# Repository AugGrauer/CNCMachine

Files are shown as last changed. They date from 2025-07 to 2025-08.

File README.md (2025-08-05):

# CNCMachine
Open source repository for the CNC machine built by [Backyard Shed Engineering](https://www.youtube.com/@ShedStuffBuiltHere)



This is a fully self-funded, opensource project done by two highschoolers. While we have tried our best to document everything, and make it as accessible as we can, there is still an aspect of DIY to this project. Before building, please study the CAD models provided. If you run into problems, open an issue and we will try to respond and improve this guide.

This machine is mostly 3D printed. 3D printer access is required. 
## License


Feel free to use this as a basis for your own project, or replicate it!

## Table of Contents
- [Specifications](#specifications)
- [License](#license)
- [BOM](#bom)
- [Use](#use)
- [Known Issues](#known-issues-)
- [Assembly](#assembly)
- [CAD Models](#cad-models)
- [Wiring](#wiring)
- [Firmware/Software](#firmwaresoftware)
- [Putting it all together](#putting-it-all-together)
- [Media](#media)
- [Contributing](#contributing-)
- [Roadmap](#roadmap)
- [Changelog](#changelog)
  
## Specifications

  Build Area: 16x18x1 in 

  Total Footprint: 
  
  Supported Materials: Aluminium, wood, plastics. (Anything softer than aluminium)

  Motors: 3x NEMA 23, 1x NEMA 17 

  Spindle: Choice Spindle/Router/VFD. Designed for a Dewalt Trim Router. Easily Modified for a Makita 1 1/4HP Router

  Control Board: Arduino UNO w/ GRBL 1.1
  
  Power Requirements: 120V

## BOM
BOM is in the repository and also here:
https://docs.google.com/spreadsheets/d/1JcS2ukq2nQpIpGEV6_Kvxhg6B4QogmMNbcgQQ2et4MQ/edit?usp=sharing

# Use
  We have created this repository in order to make our CNC project as open source as possible. We were really proud to do this project for under $1000, and we want others to be able to as well. Feel free to use this as a basis to design your own, or to simply make your own version of our machine. We have included the BOM, all of our 3D models used, and our wiring diagram, as well as a few extra resources and our advice. We have further explanations on our youtube channel. ⏯️

## Known Issues 🐛
  This machine is by no means perfect, so there are a few problems we have encountered. Below is a list of the problems and if we have found solutions
  1. Electromagnet Interference: ✅
     - This is probably the largest issue encountered during construction and inital operation. After investigating, it turns out that our buildplate, and most metal on the body of the CNC machine is actually charged. We aren't sure why or from where, but we suspect that it is something to do with our stepper motors.
     ### **FIX**
       - To fix this, we used EMI shielding along most of the long wires which run from stepper motors to the electrical box. This is included in the BOM, and we had just enough to get most of our wires shielded. We found that there were a few specific areas which were worse, especially where the EMI shielding/ wires in general come in contact with the metal frame of the machine. We solved this by insulating those specific areas with electrical tape.
  2. Bed Leveling 🟠
     - We have been unable to really solve this. It isn't a terrible issue, and certainly doesn't prevent the operation of the machine. Take this into account when slicing models/preparing to cut stuff, as there may be a few corners (at least for us) which dont cut all the way to the buildplate. By using an overcut, you can compensate for this.
      ### **FIX**
       - We don't have a 100% fix, but if you plan to overcut by .1/.2mm, everything should cut through. If you don't want to do that, it is pretty easy to break the last little layer off and get a clean part.
  3. Alarms ✅
     - This machine alarms a decent amount. Don't be too alarmed (See what I did there). If you are using UGS/GRBL like we did, you can reset and unlock the machine to continue. Usually alarms occur due to a voltage change, or a serious problem. After frequent use and learning, we found that most of our alarms occur when turning on the router. This is pretty easy to work with, as we just reset and continue. If your machine is constantly alarming, test it for voltage differences/charges in weird places. Try insulating. The limit switches are USUALLY not actually the problem.
      ### **FIX**
       - Reset and unlock machine. If that doesn't work, test and insulate/ground different areas. Limit switches are pretty reliable for us, so that was almost never the issue.
  4. Soft Limits ✅
     - These never worked on our machine. We don't know why. We just don't use them.
      ### **FIX**
       - Don't use
  5. Weird GCode ✅
     - There are a few weird little GCode quirks that we have to deal with to operate. Shown here is what the start and end of our GCode looks like. This works. Obviously it will be different depending on position, tool, etc but the start and end remain the same. Make sure your code looks similar/the same, as you run the risk of breaking a bit if not. If it looks different, I'd suggest running the code without a bit, to ensure nothing will break before cutting.
### START
```
  (10022) # Program number (Changes)
  G90 G94
  G17
  G21
  (Ramp1) #This will be different depending on your action
  T1
  S5000 M3
  G17 G90 G94
  G54
  G0 Z15 #This is critical. This MUST be before the following line. This retracts the toolhead BEFORE moving XY
  G0 X-28.057 Y-2.102 # this changes
```
### END
```
G0 Z15
    # Usually there is an extra line here. Make sure to delete that, as it homes the machine, which can break bits. 
M30
```
  ### **FIX**
  - Change GCode every time. You could also write a program to do this. We will share that if we end up doing this.

## Assembly 

  DISCLAIMER:
  
  We tried to document roughly our steps in the videos on our channel, but there are a lot of nuances and tricks needed that simply arent documented. Be prepared for sanding, and some weird assemblies. In order to cut aluminium, we had to manually machine multiple parts, such as the Z axis plates, the entire aluminium base of the buildplate, and the Z traveller mount. We do not recommend this for entry level builds. If you have some time, a 3D printer, and some experience in the STEM/3D printing fields, this is very doable. All of the parts we used are in the BOM, and if you follow the 3D model, it should be pretty straight forward. It took us a total of 35 hours to build this machine, but we were doing other things and not 100% focused for much of it, in addition to having to test multiple parts. If you have questions, reach out to us via youtube, or create an issue here. We recommend looking at some youtube tutorials for parts you don't quite understand. There are great ones which let us teach ourselves GRBL and Fusion 360 manufacturing/slicing. 

## **We have created a guide which outlines the assembly as best we can. Find it in AssemblyGuide.md**

Use this guide, with the 3D model, youtube videos, and 3d model guide, to get the best idea of how to build this.

  A few notes.
  - Screws are mostly M4. The rails use M5x16 screws, and there are a few random M3 screws in there, but the majority are M4.

### CAD Models:
  [Found Here](https://github.com/AugGrauer/CNCMachine/tree/c9973d6ad02c3cf29ccf315ba2bd43aa739bddab/3D%20Models](https://github.com/AugGrauer/CNCMachine/tree/823ef2db97a0531feb1171109dd2441a3dbac2b9/3D%20Models))
  
  Our CAD models are categorized by:
  - Imports (This is largely just parts we used to build the machine)
  - Parts (Actual parts we made which were either machined or cut)
  - Assemblies (Larger models, such as the Base and Z axis)
  
### Wiring:
[Found Here](https://github.com/AugGrauer/CNCMachine/tree/c9973d6ad02c3cf29ccf315ba2bd43aa739bddab/Wiring](https://github.com/AugGrauer/CNCMachine/tree/823ef2db97a0531feb1171109dd2441a3dbac2b9/Wiring))

  We have provided our wiring diagram above. We also created a custom electrical box for these wires, but that is entirely optional. See docs in wiring folder for more info. 
  
### Firmware/Software:
  This machine runs off of GRBL and Universal GCode Sender. Below are the downloads:

  [GRBL](https://github.com/grbl/grbl)

  [UGS](https://winder.github.io/ugs_website/)

  We changed our GRBL config file before uploading to the Arduino. Make sure to get all the pin numbers correct. (Found in cpu_map.h)
  
  For UGS, we did not change much. Go through the Setup Wizard and ensure your machine passes all checks. Be sure to test limit switches and tune steps/mm for the steppers.

### Putting it all together:
  When it comes down to it, theres a few key steps to follow:
  
1. Order/Print parts
2. Assemble hardware
3. Wire based off of our guide
4. Flash GRBL
5. Troubleshoot and Test UGS

Follow AssemblyGuide.md but if you have questions, please create an issue here, leave a comment on our videos, or even email us.

Here is the link our video playlist explaining it: https://www.youtube.com/watch?v=x9RqWOT4NOQ&list=PLWdkqCAyfFqSBZGNOKGVb3XG4A6ohDbLp

## Media

CAD:

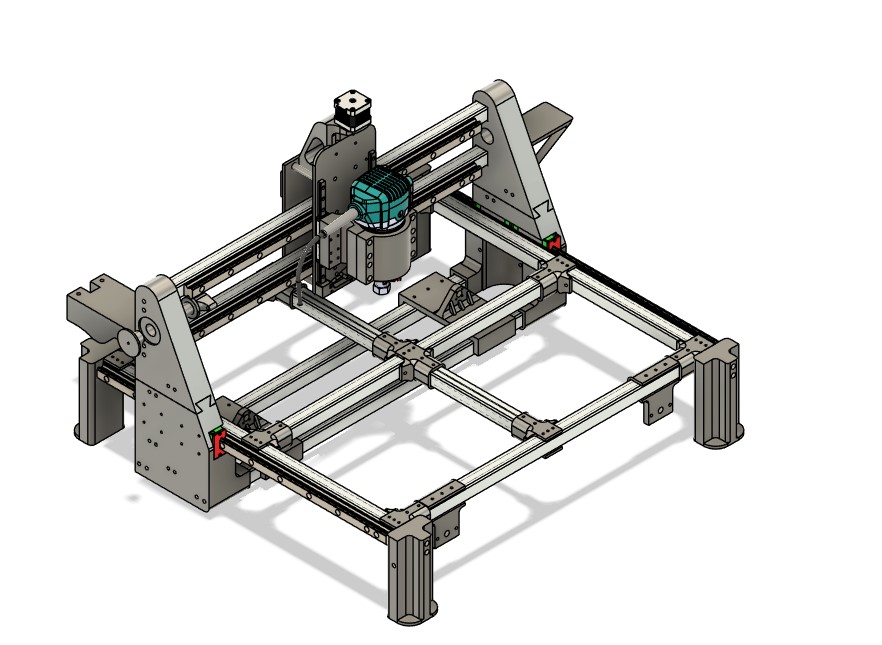
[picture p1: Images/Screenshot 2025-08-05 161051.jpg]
/Images/Screenshot 2025-08-05 161051.jpg)
)

Base:

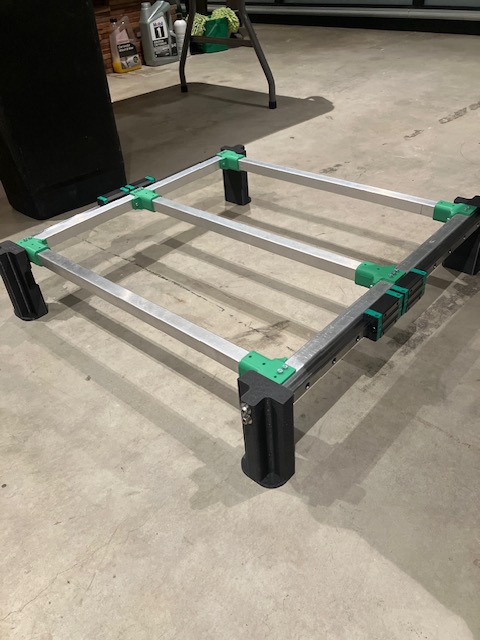
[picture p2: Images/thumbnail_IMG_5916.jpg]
base


In Progress:

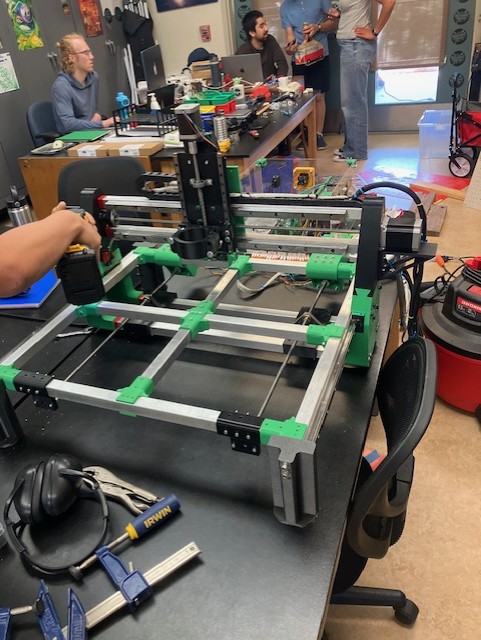
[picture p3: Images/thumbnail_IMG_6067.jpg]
progress


Full build:

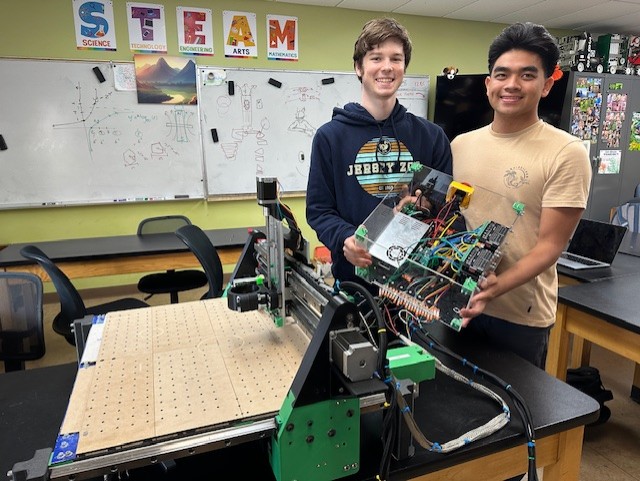
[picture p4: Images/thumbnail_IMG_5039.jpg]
full)


## Contributing 🔨
  We welcome any progress, changes, and suggestions. We definitely want to improve and build upon both this machine and open source project.

## Roadmap
  - Design Dust collection/cleaning system
  - Automate spindle cooling/oil dripping
  - Explore VFD possibilites
  - Create a GCode Pre-processor to speed up work

## Changelog
  # V 1.0
  - Initial open-source release
  - Complete with BOM, CAD models, wiring diagrams, and build videos

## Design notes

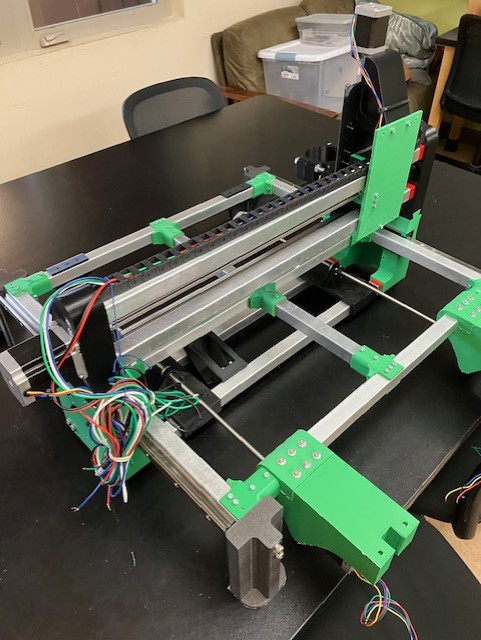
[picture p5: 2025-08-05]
Images/thumbnail_IMG_6022.jpg

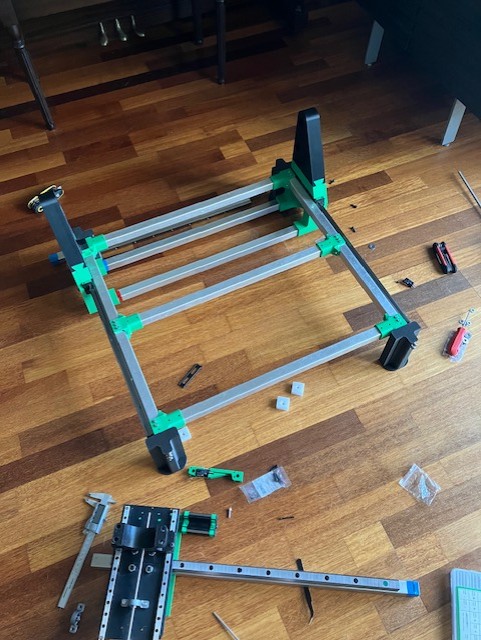
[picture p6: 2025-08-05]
Images/thumbnail_IMG_5942.jpg

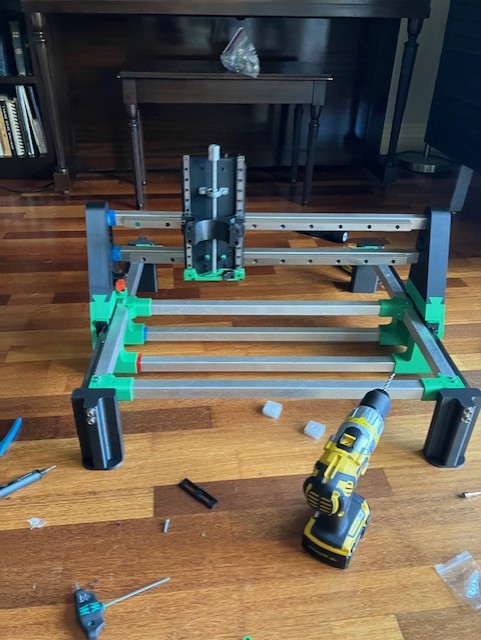
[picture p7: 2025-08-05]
Images/thumbnail_IMG_5947.jpg

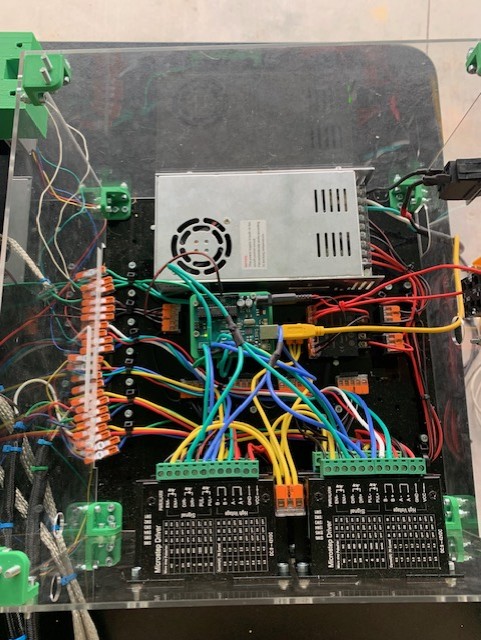
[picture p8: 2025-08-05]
Images/thumbnail_IMG_3427.jpg

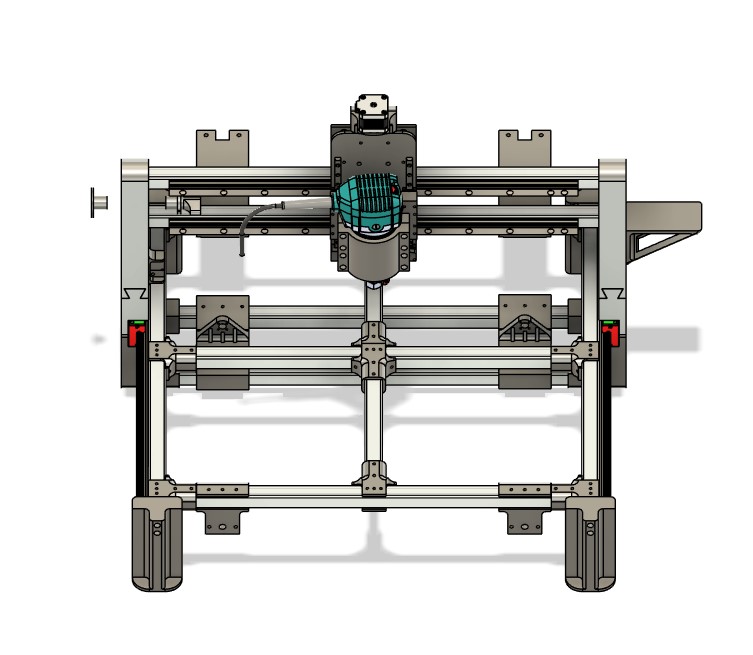
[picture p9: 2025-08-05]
Images/Screenshot 2025-08-05 161105.jpg

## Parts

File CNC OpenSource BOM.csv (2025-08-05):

Item | Supplier | Amount | Price per | Price total | Link | Column 1
NEMA 23 Stepper Motors, Drivers, and PSU | Amazon | 1 | $131.00 | $131.00 | https://www.amazon.com/RATTMMOTOR-Controller-Nema23-Stepper-Control/dp/B09MRYBNTX
250mm Leadscrew | Amazon | 1 | $19.84 | $19.84 | https://www.amazon.com/Vertical-Printer-Bearing-Flexible-Coupling/dp/B0B8WR5R8W?gQT=1&th=1
600mm LeadScrew | Amazon | 2 | $38.70 | $77.40 | https://www.amazon.com/100-600mm-Bearing-Bracket-Flexible-Coupling/dp/B0DMJDKH3Z?gQT=1&th=1
650mm LeadScrew | Amazon | 1 | $20.99 | $20.99 | https://www.amazon.com/ReliaBot-650mm-Thread-Starts-Printer/dp/B092W56RC4?gQT=1
Emergency Stop | Amazon | 1 | $9.99 | $9.99 | https://www.amazon.com/Baomain-Emergency-Switch-Button-Weatherproof/dp/B00NTT91Y0?hvadid=695397056053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
HGR20R 600mm | Amazon | 2 | $50.99 | $101.98 | https://www.amazon.com/Linear-20-600mm-Bearing-Guideway-Routers/dp/B0BKGB99SD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
Limit Switches | Amazon | 1 | $6.39 | $6.39 | https://www.amazon.com/Cylewet-V-156-1C25-Momentary-Arduino-CYT1046/dp/B06WRN7FQB
MGN9 250MM carriage and rails | Amazon | 1 | $28.88 | $28.88 | https://www.amazon.com/gp/product/B09QYMQW5V/ref=ox_sc_act_title_1?smid=A3BJIOXQCA1C52&th=1
Power Step | Amazon | 1 | $9.99 | $9.99 | https://www.amazon.com/EPBOWPT-Converter-Regulator-Voltage-Transformer/dp/B0DPZYH3C7
6061 T651 Aluminum Sheet Metal 12 x 12 x 0.20 (5mm) Inch Flat Plain Aluminum Plate Covered with Protective Film, Heat Treatable Rectangle Aluminum Metal Plate for Crafting, DIY, Industrial | Amazon | 1 | $22.99 | $22.99 | https://www.amazon.com/Aluminum-Protective-Treatable-Rectangle-Industrial/dp/B09JFN8353
1/4 in shank 1/8 in cutting bit | Amazon | 1 | $16.99 | $16.99 | https://www.amazon.com/dp/B0D1DS85TK?ref=ppx_yo2ov_dt_b_fed_asin_title&th=1
Extra Stepper motor driver | Amazon | 1 | $10.89 | $10.89 | https://www.amazon.com/dp/B08SG7L54W?ref=ppx_yo2ov_dt_b_fed_asin_title
Wago Multipack | Amazon | 1 | $14.77 | $14.77 | https://www.amazon.com/dp/B07NKSHVF6?ref=ppx_yo2ov_dt_b_fed_asin_title
16 AWG Wire | Amazon | 1 | $16.99 | $16.99 | https://www.amazon.com/dp/B0CMLFRQDQ?ref=ppx_yo2ov_dt_b_fed_asin_title&th=1
50mm m4 screws | Amazon | 1 | $9.38 | $9.38 | https://www.amazon.com/dp/B089NJRS78?ref=ppx_yo2ov_dt_b_fed_asin_title&th=1
Solid lead screw couplers | Amazon | 2 | $8.99 | $17.98 | https://www.amazon.com/Befenybay-Coupling-Diameter-Coupler-Aluminum/dp/B07WZJSLBL
nema 17 stepper motor | Amazon | 1 | $14.99 | $14.99 | https://www.amazon.com/CNCTOPBAOS-Stepper-2-Phase-17HS4218-Engraver/dp/B09FLG1VPF?xpid=Nh-QG1XuaLlTQ
2 more carriages for z | Amazon | 2 | $10.92 | $21.84 | https://www.amazon.com/KGTCN-Miniature-Sliding-Machine-Printer/dp/B0C3CSKTVN?s=industrial
electromagnetic shielding | Amazon | 1 | $17.99 | $17.99 | https://www.amazon.com/Tinned-Copper-Braided-Sleeving-Diameter/dp/B01BIBQ940
Cable chain | Amazon | 1 | $11.99 | $11.99 | https://www.amazon.com/dp/B07QVKL1H6/?coliid=I1AD8NK504AR2V&colid=39P1VAIP6UUD2
weideer 2322pcs M3 Screw Assortment Kit | Amazon | 1 | $25.99 | $25.99 | https://www.amazon.com/dp/B0DS8HYF64/
Filament 1kg | Amazon | 3 | $20.99 | $62.97 | https://www.amazon.com/Overture-Filament-Professional-Toughness-Dimensional/dp/B07YDN56F2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
Aluminum Composite panel | Amazon | 1 | $35.82 | $35.82 | https://www.amazon.com/Falken-Design-Aluminum-Composite-Brushed/dp/B07NRBGHVB?s=industrial
1501 Series M4 x 0.7mm Standoff (6mm OD, 58mm Length) - 4 Pack | GoBilda | 1 | $5.99 | $5.99 | https://www.gobilda.com/1501-series-m4-x-0-7mm-standoff-6mm-od-58mm-length-4-pack/
1/2 in bar | The Depot | 1 | $13.27 | $13.27 | https://www.homedepot.com/p/Everbilt-1-2-in-x-4-ft-1-8-in-Thick-Plain-Steel-Flat-Bar-0702/332734311
16 AWG wire x4 | The Depot | 4 | $6.63 | $26.52 | https://www.homedepot.com/p/Cerrowire-24-ft-16-Gauge-Red-Stranded-Primary-Wire-207-1203R24/202206417
Switch | The Depot | 1 | $4.96 | $4.96 | https://www.homedepot.com/p/Gardner-Bender-10-Amp-Single-Pole-Illuminated-Rocker-Black-Switch-GSW-49/300349420
Tool repair cord | The Depot | 1 | $16.68 | $16.68 | https://www.homedepot.com/p/Husky-9-ft-14-3-Medium-Duty-Tool-Replacement-Cord-Black-HD-342-576/303679849
M5x16 screws 2pc | The Depot | 12 | $2.25 | $27.00 | https://www.homedepot.com/p/5-mm-0-8-x-16-mm-Internal-Hex-Plain-Steel-Metric-Socket-Cap-Screw-2-Pieces-803288/204274287
Lag Bolts for router clamp | The Depot | 4 | $3.75 | $15.00 | https://www.homedepot.com/p/M8-1-25-x-50-mm-Class-8-8-Zinc-Plated-Hex-Bolt-801718/204273672
Nuts for router clamp | The Depot | 2 | $3.75 | $7.50 | https://www.homedepot.com/p/Everbilt-M8-1-25-Zinc-Metric-Hex-Nut-5-per-Bag-802418/204281770
Wago direct conenctors | The Depot | 1 | $21.97 | $21.97 | https://www.homedepot.com/p/WAGO-221-2401-Lever-Nuts-Inline-2-Wire-Splicing-Connectors-25-Pack-0221240K000-0012/330518029
Peanut Bar 72 in | Other | 3 | $29.00 | $87.00 | https://andymark.com/products/1-x-1-peanut-extrusion-different-lengths?variant=44493385990316 | This gets cut into rougly 2 foot sections
Cut Board (Draftboard) | The Depot | 1 | $6.49 | $6.49 | https://www.homedepot.com/p/ProWood-1-8-in-x-2-ft-x-4-ft-Tempered-Hardboard-Actual-0-115-in-x-23-75-in-x-47-75-in-Project-Panel-109112/202585358
 |  |  | Total | 940.42 | Plus Tax

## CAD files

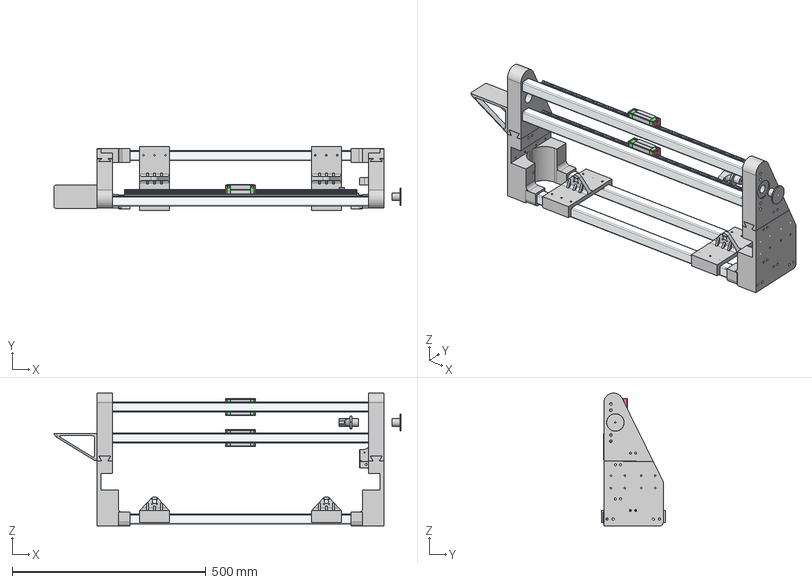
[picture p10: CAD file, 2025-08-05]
3D Models/X/full x gantry model v3.step
895.6 x 165.4 x 343.2 mm
Component1(Mirror)(Mirror) (2)(Mirror)
Component1(Mirror)(Mirror) (2)(Mirror)_1
xAxisMotorMount
am-3090a-2 2ft Peanut x 2
am-3090a-2 2ft Peanut_1 x 2
HGR20R LINEAR GUIDE RAIL, CONFIGURABLE, 600 mm x 2
HGH20CAZ0C, BLOCK, MIDSECTION x 2

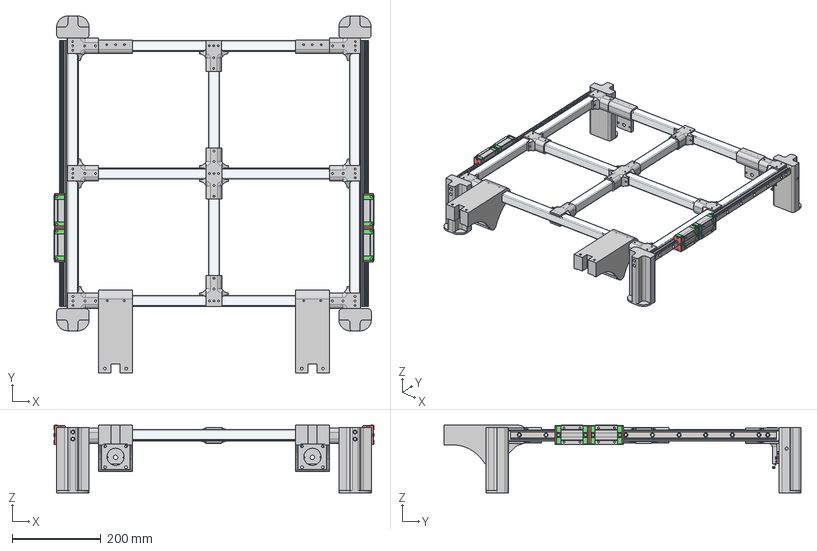
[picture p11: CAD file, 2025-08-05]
3D Models/B/base.step
720.8 x 804.6 x 152.8 mm
Component1(Mirror) (2) x 2
HGR20R LINEAR GUIDE RAIL, CONFIGURABLE, 600 mm
HGR20R LINEAR GUIDE RAIL, CONFIGURABLE, 600 mm_1
HGH20CAZ0C, BLOCK, MIDSECTION x 2
HGH20CAZ0C, BLOCK, MIDSECTION v1(Mirror) x 2
leg3
Cover
Connector - straight x 2
Connector - bent
Switch
Rivet - long
Arm
Roll
Rivet - short
leg3 v7
leg3 v3(Mirror)
leg3 v3(Mirror)(Mirror)
am-3090a-2 2ft Peanut x 2
Component1(Mirror) (1)
am-3090a-2 2ft Peanut_1 x 3
am-3090a-2 2ft Peanut_2 x 2
y leadscrewholder endstop x 2
Component1(Mirror) (3)
Component1(Mirror) (4) x 3
Component1(Mirror) (5)

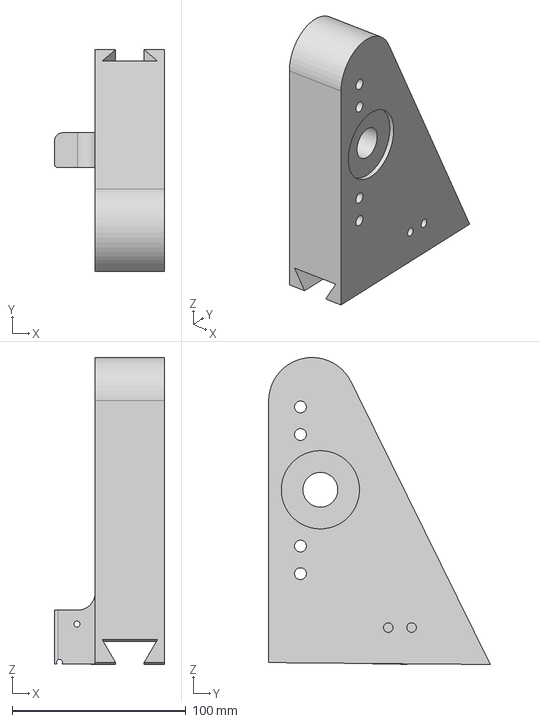
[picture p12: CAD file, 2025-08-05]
3D Models/X/right x wall top v1.step
63.4 x 127.5 x 176.5 mm

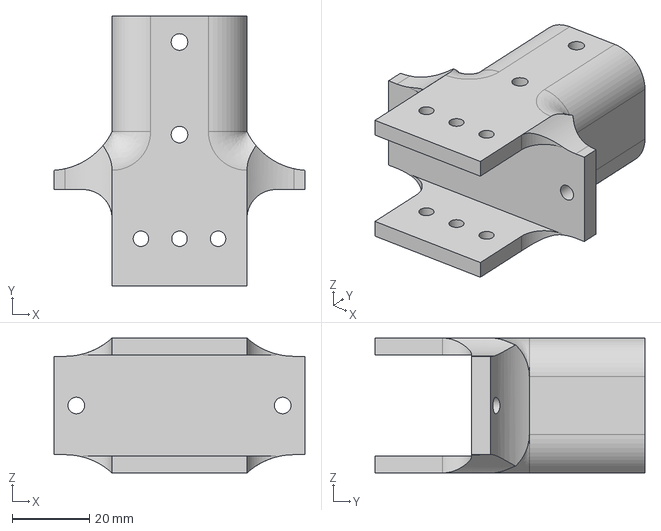
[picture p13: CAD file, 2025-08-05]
3D Models/B/side coupler_.step
65.0 x 70.0 x 35.0 mm

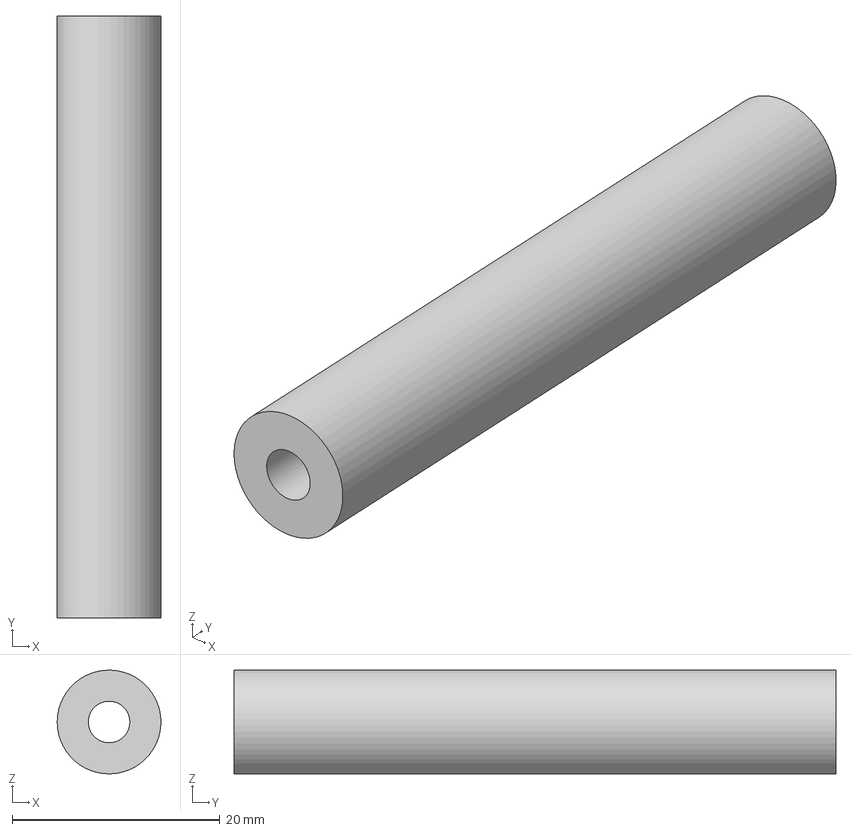
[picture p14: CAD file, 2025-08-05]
3D Models/Z/z spacer (standoffs) v1.step
9.99 x 58.0 x 10.00 mm

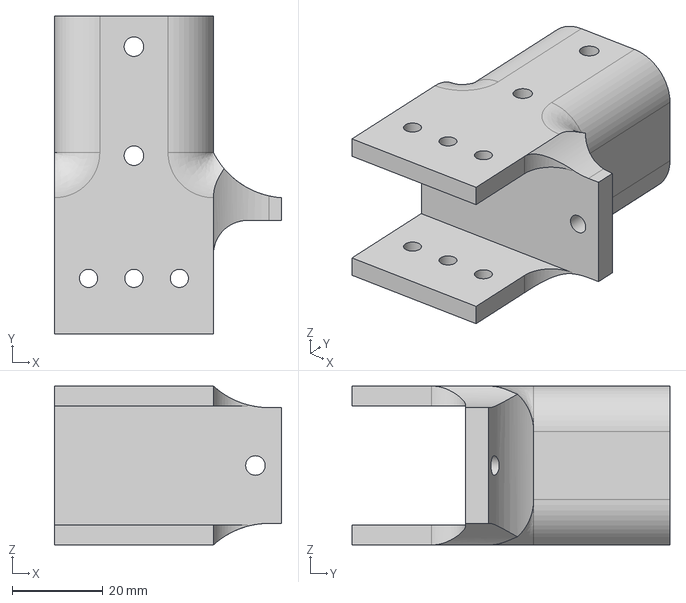
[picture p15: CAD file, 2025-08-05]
3D Models/B/corner coupler_.step
50.0 x 70.0 x 35.0 mm

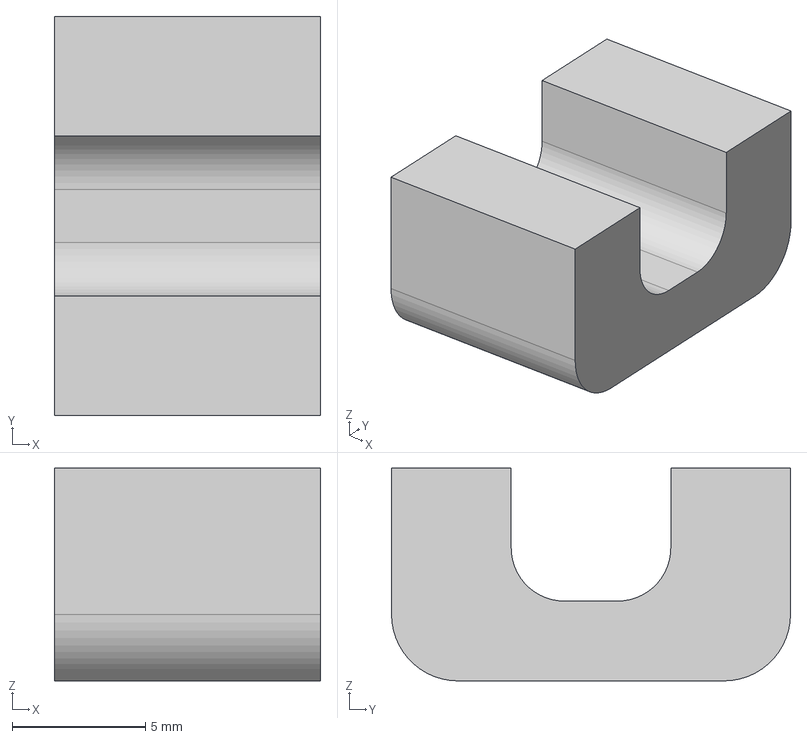
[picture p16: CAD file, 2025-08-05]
3D Models/X/cable holder v4.step
10.0 x 15.0 x 8.00 mm

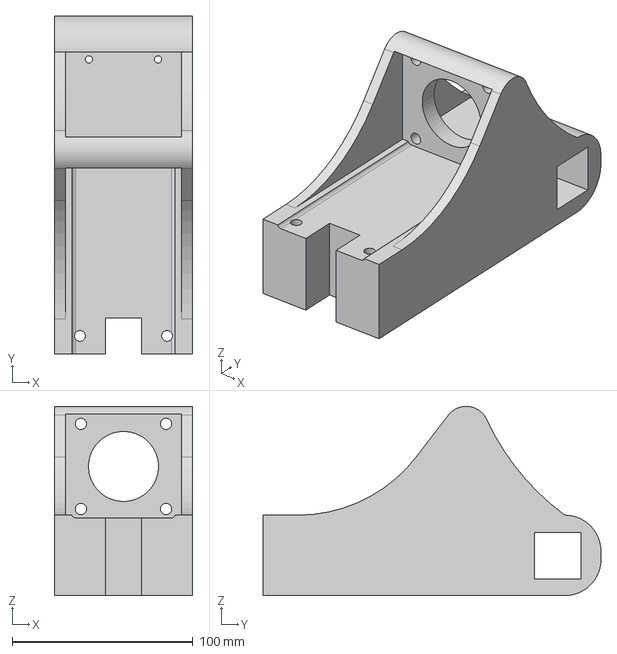
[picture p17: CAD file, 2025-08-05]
3D Models/Y/y motor mount L&R v3.step
76.4 x 186.9 x 104.6 mm

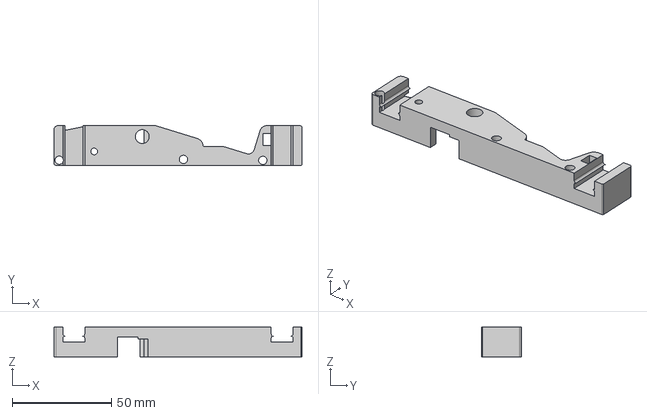
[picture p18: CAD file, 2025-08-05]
3D Models/Z/limit switch holderend stop v1.step
125.0 x 20.0 x 15.0 mm

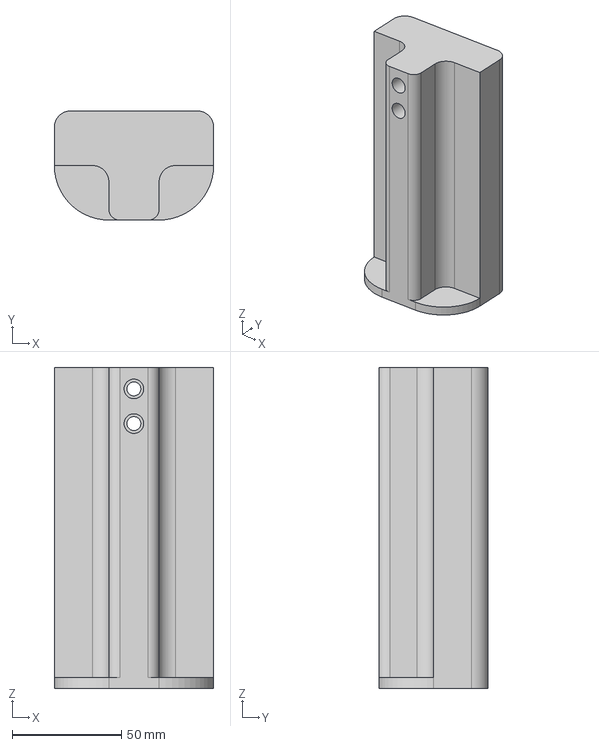
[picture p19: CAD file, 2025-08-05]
3D Models/B/normal leg_.step
73.0 x 50.0 x 147.0 mm

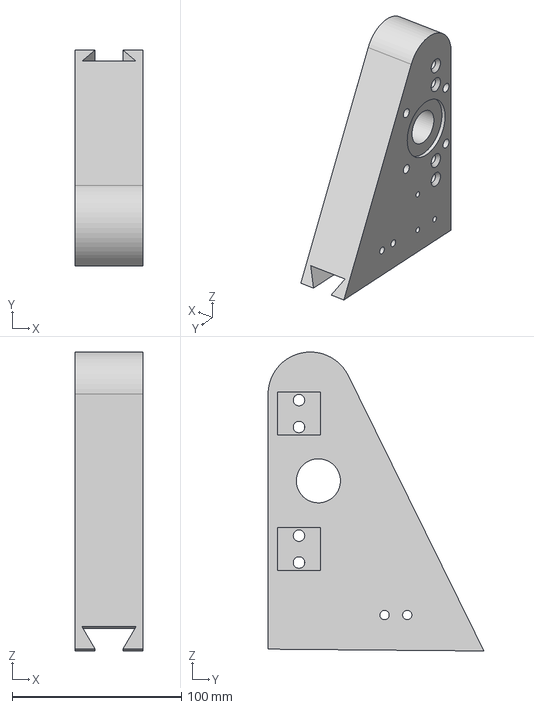
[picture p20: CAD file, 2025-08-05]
3D Models/X/left x wall top v2.step
40.0 x 127.5 x 176.5 mm

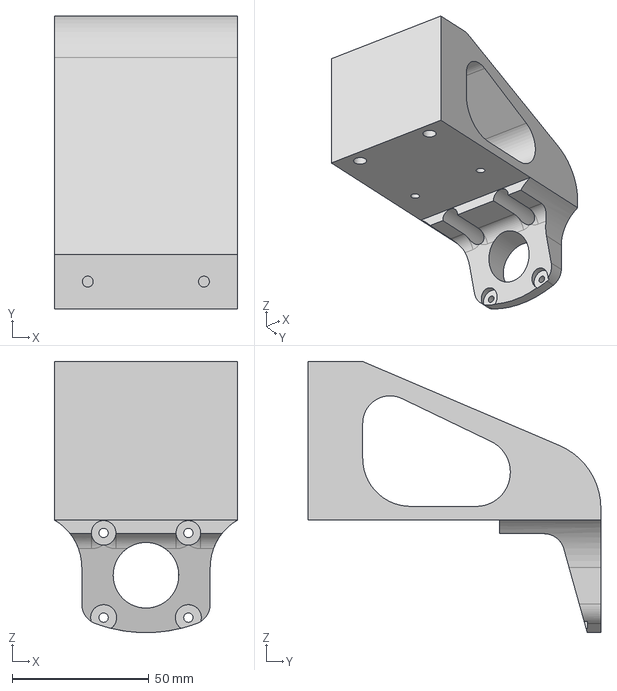
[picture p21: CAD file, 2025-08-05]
3D Models/Z/overhead z stepper motor mount v1.step
67.0 x 107.1 x 99.1 mm

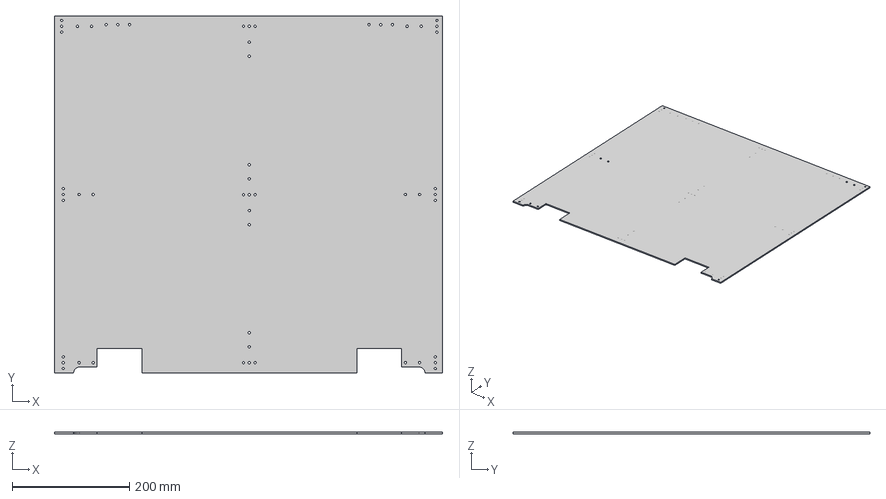
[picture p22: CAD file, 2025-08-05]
3D Models/B/Composite base plate_.step
662.7 x 609.6 x 3.17 mm

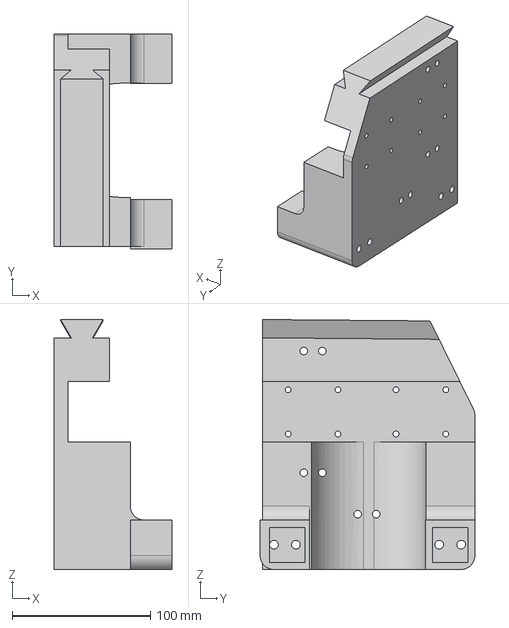
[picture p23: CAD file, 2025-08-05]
3D Models/X/left x wall bottom v1.step
85.0 x 155.2 x 180.8 mm

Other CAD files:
3D Models/Z/z back plate stencil v1.step
3D Models/B/4way_.step
3D Models/Z/front router clamp v1.step
3D Models/B/limit switch leg_.step
3D Models/B/4way.f3d
3D Models/B/Slide hole center.f3d
3D Models/B/Slide hole center_.step
3D Models/B/composit base plate.f3d
3D Models/B/corner coupiler.f3d
3D Models/B/limit swich leg.f3z
3D Models/B/normal leg.f3d
3D Models/B/side coupiler.f3d
3D Models/X/cable holder.f3d
3D Models/X/left inner wall leadscrew endstop v1.step
3D Models/X/left inner wall leadscrew endstop.f3d
3D Models/X/left outer wall leadscrew endstop v1.step
3D Models/X/left outer wall leadscrew endstop.f3d
3D Models/X/left x wall bottom.f3d
3D Models/X/left x wall top.f3d
3D Models/X/right x wall bottom v1.step
3D Models/X/right x wall bottom.f3d
3D Models/X/right x wall top.f3d
3D Models/X/xAxisMotorMount v2.f3z
3D Models/X/xAxisMotorMount v2.step
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

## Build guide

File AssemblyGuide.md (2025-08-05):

Here we have outlined a rough build guide. Refer to 3D model as needed

# OVERVIEW
### Step 1. Base & Y Axis mounts
### Step 2. Z Axis
### Step 3. X gantry

## STEP 1.  BASE

### Parts Made:
To build the base of this machine we first cut the peanut bar into the following:

	2x 609.6mm (2ft) bars
	3x 600mm bars
	2x 252.25 mm bars
We also printed:

	3x Normal leg
	1x Limit switch leg
	1x 4 way coupler
	4x Corner coupler
	4x Side coupler
	2x Y Axis Motor Mount
	2x Y Axis Leadscrew endstop
	2x C clamp assist (Optional)
	2x Slide hole center (Optional)
### Assembly
  	1 Mount the linear slides to the 2 foot bars. We made sure that the slides would be mounted so that the slides would be mounted perpendicular to the peanut bar holes. We used our 2 C clamp assist prints to center the slide on the bar, then made sure the rail was centered from end to end on the bar (Same distance from the end of the bar to the start of the slides on each side). We used a hole punch and our Slide hole center prints to make sure we were making the holes in the center of our slides. We then removed the slides, then drilled and tapped all the holes for M5 screws. 
  
  	2 Install the slides. Screw in with M5x16 screws. Do this for both sides of the base.
  
  	3 At this point, we assembled the whole base. It all goes together, it's just a little tricky. Take one side, and put the corner couplers flush in each corner. Attach a side coupler to the center of the bar, and prepare to attach all of these in (Drill and tap holes, don’t screw in yet.). Attach 252.25mm bars to opposing sides of the 4 way couplers so that you can slide it to the middle of the centermost bar (600mm), which should be attached to the side coupler. 
  
  	4 Put side couplers on the exposed ends of the 252.25mm bars. Slide the remaining 2 600mm bars into the corner couplers on the already assembled side. Assemble the second set of corner couplers and singular side coupler onto the other bar with slides, and push it all together. The center bar should go across the machine (see model), and be as centered as possible. 
  
  	5 Mount the Y axis motor mounts flush with the corners. Install Y axis Stepper motors. Install the Y Axis Leadscrew mounts to be in line with the center hole of the Y axis motor mounts.
  
  	6 At this point, you should install the aluminium composite buildplate. Cut this to size, and ensure it fits your machine. Use the holes/ screw locations for the couplers to attach everything securely (aluminium compost and also couplers at the same time.. (Drill, and tap, using M4 screws to attach).
  
  	7 The base is nearly done. Now, slide the carriages onto the Y slides. Ensure that you have removed a screw from the side of each carriage so they go flush. There should be 2 carriages on each slide.
  
  	8 Finally, install the legs. Screw these into the end of each peanut bar, ensuring the leg with a limit switch cutout is in such a position where it will work. For us, it was in the back left of our machine. 

## STEP 2: Z AXIS 

The Z Axis is a pretty important part. We chose to hand cut a lot of components for this out of aluminium, to ensure its rigidity and reliability. We also have 3d models for this to act as stencils or maybe work instead. 

### Parts Made:

	1x back router clamp
	
 	1x front router camp 
	
 	1x Z Limit switch holder
	
 	1x Z stepper holder

	8x Z screw spacer
 
	1x Z Front plate (Aluminium, Stencil?)
 
	1x Z Back plate (Aluminium, Stencil?)
 
	1x x nut holder (Aluminium, Stencil?)

  	3x Z spacers (standoffs)
### Assembly

	1 Screw in the linear rails along the side. Ensure that there are 2 carriages on each rail.This installation used M3-M3.5 Screws (See multipack). These should line up with the holes in the Z front plate.
	
 	2 Next, we screwed in the leadscrew, which should fit in the predefined holes.
	
 	3 Mount the back router clamp onto the carriages. 
	
 	4 Mount the Z limit holder onto the bottom of the Z Front plate. 
	
 	5 Attach the carriages to the back of the Z front plate using M5X16 screws and the Z axis screw spacers. 
	
 	6 Attach Leadscrew nut/traveller to the x nut holder. 
	
 	7 Connect the Z front plate and the Z back plate by attaching the Z axis stepper holder and the x nut holder. We used 2 5mm plates of aluminum to create the x nut holder. Using the stencil, we screwed them together tightly with M3.5 screws and drilled holes in the side to attach, then mounted it to the machine immediately. This is weird so ask us any questions. Also connect this all with the Z spacers (standoffs) in bottom 3 holes.
	
 	8 Mount stepper motor.

## STEP 3: ½ OF X GANTRY

To attach this all, we need to install half the X gantry first. 
### Parts Made:
	1x Right x wall bottom

	1x Left x wall bottom

	1x Left x wall top
	
	1x Right x wall top

	1x xAxisMotorMount

	2x Y leadscrew nut holder

	4x 2ft peanut bars
 
	1x Left inner wall leadscrew endstop
 
	1x Left outer wall leadscrew endstop

We also used our ½ in bar and cut 

	1x 160mm stiffener
 
	2x 100mm stiffener
 
  These are optional for structure

### Assembly 
  	1 Connect the top and bottom of the right side using the dovetail. Screw in the xAxisMotorMount. Use the optional stiffener on this step to lock the dovetail in place on the side. You could also glue or epoxy this to keep it together. 
  
  	2 Construct 2 more linear rail+ peanut bar sets. See base assembly for how we did this. 
  
  	3 Put Y leadscrew nut holders across the bottom 2 peanut bars, x mm away from the edge of the bars. Screw these in with 50mm screws through the bars, ensuring that they are not on the same side as the peanut bar holes.
 
  	4 Push in bottom peanut bars, in addition to the top ones with the rails. Screw these in on the sides. Make sure peanut bar holes line up. 
 
  	5 Construct the other side of X gantry. Use the bottom side with the limit switch holder, and another Top X gantry side. Attach together with the same previous method.
  
  	6 Put the Z axis assembly onto the rails of the X gantry. 
  
  	7 Line both sides up with their respective Y Carriages, which are already mounted on the base. Push together, ensuring that the X gantry stride with peanut bars attached fits nicely into the other side. Line holes up with Y carriages again, and mount using M5x16 screws. Screw peanut bars on the opposite side
  
  	8 Attach X stepper to X leadscrew using clamp, then push through hole on X gantry side. Make sure it goes through the traveller, then into the Left leadscrew endstop (Use the two parts of this to clamp the inside and outside), which is attached opposite the stepper motor. (The stepper motor should be on the stepper holder). Secure stepper motor. 
  
  	9 Push Y lead screws through the bottom nut holder located on the bottom of the X gantry. Secure to stepper motor. 
   	
    	10 Add the wire holders spaced along the bottom of the X gantry. You'll want to already have the wire in here if you plan to do it this way. Next, attach the cable chain to the top X bar.

# NOTES:
Follow the CAD model and videos as you go. Between this and those resources, it should hopefully be clear what to do.

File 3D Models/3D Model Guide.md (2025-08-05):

# 3D Model Guides

Full assembly is in the main folder, and subassemblies in their respective ones. We used Overture SuperPLA+ and PLA professional for this project.

## B - Base
## X - X Axis
## Y - Y Axis
## Z - Z Axis

## B

  4way: 4 way coupler for base
  
  Composite base plate: stencil/ idea for your baseplate, maybe make your own
  
  Corner coupler: coupler for the corners of the CNC
  
  Side coupler: coupler for the sides of the CNC
  
  Normal leg: leg without limit switch
  
  Limit switch leg: leg with limit switch.

  Slide hole center: center little thing to center hole punch in rails/slides

## X
  
  Left inner wall leadscrew endstop: Inside wall side of the extender which attached to the X leadscrew
  
  Left outer wall leadscrew endstop: Clamps to the inner wall endstop
  
  Left x wall bottom: Bottom X gantry wall for the left side
  
  Left x wall top: Top X gantry wall for the left side
  
  Right x wall bottom: Bottom X gantry wall for the right side
  
  Right x wall top: Top X gantry wall for the rightside
  
  xAxisMotorMount: Motor mount/support for the X axis stepper motor.

## Y
  
  y leadscrewholder endstop: Endstop for the y axis leadscrew. 2x used. 
  
  y lead screw nut holder (L&R): Holder which attaches to bottom of X gantry, holds the travellers for the Y leadscrews
  
  y motor mount (L&R): Mounts for both Y axis stepper motors.

## Z

  back router clamp: The back of the clamp which holds the router. Attached to Z carriages
  
  front router clamp: Front of router clamp, attached with big bolts
  
  limit switch holder/end stop: holds limit switch for Z and acts as end stop
  
  overhead z stepper motor mount: Mount for Z stepper
  
  x nut holder: Holds traveller for X axis onto Z assembly
  
  z back plate stencil: stencil for Z back plate, 3dp or laser cut
  
  z front plate stencil: stencil for Z front plate, 3dp or laser cut

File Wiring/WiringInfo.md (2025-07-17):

# **HERE IS THE LINK TO THE WIRING DIAGRAM**

https://miro.com/app/board/uXjVIAJd17c=/?share_link_id=497290069318

## Use
  This wiring diagram is what is currently on our operating CNC machien that was covered in the videos. The wires are roughly color coded (Best I could do). Red is for +, Black is for GND. The rest are signal wires, but all of them should be different distinct colors. The large squares/boxes in the diagram represent WAGO connectors, with the largest being 5 wire connectors, and the smallest being 3 wire connectors. Let us know about any issues. The stepper motor wiring is the exact same for every single one. The funky wiring for the Z stepper motor ground is just a product of us not having enough WAGOs. To power the Arduino, we used a male DC power jack to the Arduino input. 

## GRBL Pins
  We used GRBL 1.1 for this machine. The pins on the arduino need to be configured to your specfic setup. This is found in config.h, which you should edit before pushing to the arduino. There are many tutorials online on how to use/upload GRBL. 
  
## Makita Router
  In order to make it work with a Makita router, we also added a grounding strap, which was simply one wire connected to an open WAGO ground port, which we stuck the other end into a grounded rod. Another wire was connected to the other open ground port, from there it has a Y-lead to ground both the router and the buildplate.

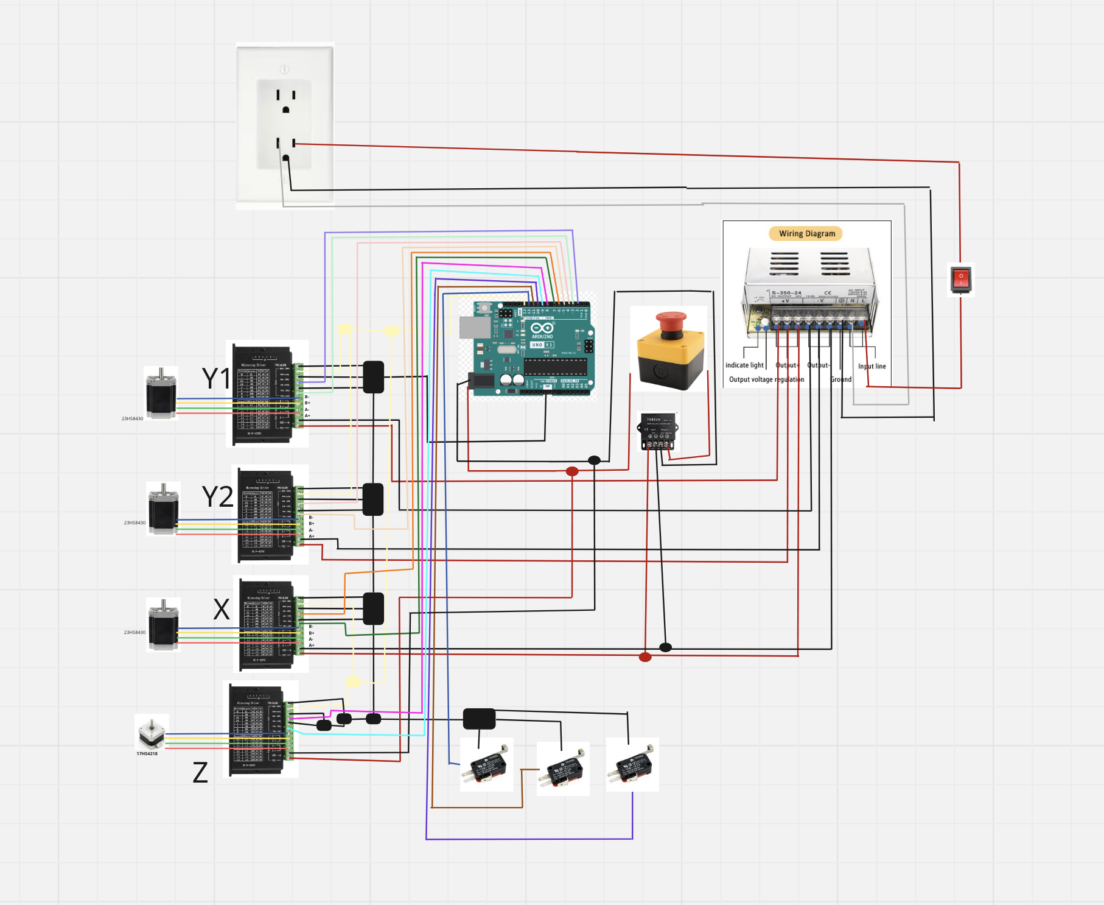
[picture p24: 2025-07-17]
Wiring/WiringDiagram.png

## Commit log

2025-07-16 Create WiringAdvice
2025-07-16 Update and rename WiringAdvice to WiringInfo.md
2025-07-17 Create BOM
2025-07-17 Update and rename CNC OpenSource BOM - BOM.csv to BOM
2025-07-17 Update and rename BOM to BOM.csv
    [BOM.csv]
2025-08-05 Create AssemblyGuide
2025-08-05 Update and rename CNC OpenSource BOM - BOM (1).csv to CNC OpenSource BOM.csv
    [CNC OpenSource BOM.csv]

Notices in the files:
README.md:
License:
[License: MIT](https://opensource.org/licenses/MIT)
